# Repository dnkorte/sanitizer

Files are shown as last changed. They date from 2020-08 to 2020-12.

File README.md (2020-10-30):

# Hand Sanitizer Dispenser

<h1 align="center">
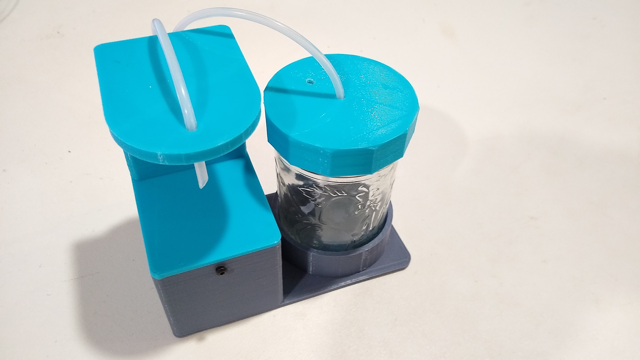
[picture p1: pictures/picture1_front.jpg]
Picture of Hand Sanitizer Dispenser
	<br>Hand Sanitizer Dispenser
</h1>

Hand Sanitizer (or soap) dispenser uses peristaltic pump to dispense fluid when Adafruit VCNL Optical Proximity Sensor observes hand under dispensing tube.  Code runs on an Adafruit ItsyBitsy 32u4 5v version (which may be powered by 12v Vbat) and is coded in Arduino IDE.  This is all packaged in a 3d printed container, and uses a standard Jelly Jar to hold the fluid.

Video of dispenser in action:  https://youtu.be/iYxsz3DUehM 

Photo Album: https://photos.app.goo.gl/EdRW3g8P56AdBAn6A

Thingiverse with STLs: https://www.thingiverse.com/thing:4636984

Some photos of the device are in the "photos" folder here on github; a larger collection is available in the linked photo album.  The Arduino software is in the "dispenser" folder here.  Printed Circuit board gerber files and schematic are in the "hardware" folder. STLs for 3d pringing are available in the "3d_printer_stls" folder and also on Thingiverse.   Note that it is important to use only the 5 Volt version of the 32u4 Itsy Bitsy, as this device allows a wider range of power input (the 5v 32u4 allows up to 16 volts input, but the normal ones only allow 6v input.  This circuit powers the Itsy Bitsy from the same 12v power block that runs the motor).

The device is setup such that when you initially put a hand into the dispense window it starts pumping at a high rate, then after a couple cycles it slows down for the balance of the hand-in-window period.  This helps to initially prime the pump/hose if its been sitting for a while, but doesn't over-deliver once its gotten started.  When the hand is removed it reverses the motor and sucks back some fluid to reduce drippage.

The device plays a series of beeps through the included speaker while it is dispensing.  

### Bill of Materials

| Description | Supplier | Notes |
| --- | --- | ----- |
| [ItsyBitsy 32u4 5v](https://www.adafruit.com/product/3677) | Adafruit | must be 5v version for power supply [Guide](https://learn.adafruit.com/introducting-itsy-bitsy-32u4/overview) |
| [TB6612 Motor Driver](https://www.adafruit.com/product/2448) | Adafruit | [Guide](https://learn.adafruit.com/adafruit-tb6612-h-bridge-dc-stepper-motor-driver-breakout) |
| [VCNL 4040 Lux/Proximity Sensor](https://learn.adafruit.com/adafruit-vcnl4040-proximity-sensor/) | Adafruit | [Guide](https://www.adafruit.com/product/4161)
| [2.1mm Barrel Jack](https://www.adafruit.com/product/610) | Adafruit |
| [Mini Oval Speaker](https://www.adafruit.com/product/3923) | Adafruit | note: will cut off connector and replace |
| [Peristaltic Pump 12v with hose](https://www.amazon.com/Peristaltic-Liquid-Dosing-Silicone-Tubing/dp/B075VN1QZM) | Amazon | includes 1m silicone tubing & 2 barbed connectors; 100 mL/min 300 mA |
| [12v 2A power supply with Barrel plug](https://www.amazon.com/TMEZON-Power-Adapter-Supply-2-1mm/dp/B00Q2E5IXW) | Amazon  |
| [2-pin Screw Terminal Block](https://www.amazon.com/dp/B01C3DGIBQ/) | Amazon | 2 pcs req'd; 3.5mm pitch |
| [47 uF Electrolytic Capacitor](https://www.adafruit.com/product/2194) | Adafruit | stand-up tubular, value not critical, just for DC blocking
| [Female Header Strip](https://www.adafruit.com/product/598) | Adafruit | need  to cut 2 14 pin sections |
| [Pin Header strip (male)](https://www.adafruit.com/product/392) | Adafruit | need to cut 3-pin, and 4-pin sections |
| [2-pin Dupont Connector body](https://www.amazon.com/Hilitchi-2-54mm-Headers-Connector-Housing/dp/B012EOO9Q0/) | Amazon | with female pins (note this assortment has 2- and 4- pin bodies as well as male pin header strip; you will need a [crimper](https://www.adafruit.com/product/350) to assemble these)|
| [4-pin Dupont Connector body](https://www.amazon.com/Hilitchi-2-54mm-Headers-Connector-Housing/dp/B012EOO9Q0/) | Amazon | with female pins |
| M3 x 8mm screws | Amazon | 12 pcs (lid-to-box, hose clamps to tower, tower-to-lid) |
| M3 x 6mm screws | Amazon | 4 pcs (to mount PCB) |
| M2.5 x 6mm screws | Amazon | 4 pcs (for Proximity Sensor) |
| [M3 Threaded Insert](https://www.mcmaster.com/94459A130/) | McMaster-Carr | 14 pcs (lid-to-box, hose clamps, pump, PCB-to-box) |
| [M2.5 Threaded Insert](https://www.amazon.com/Products-Insert-Heat-Sink-Injection/dp/B07HKT5W7S/) | Amazon | 4 pcs (for Proximity Sensor) |
| Glass Jelly Jar | local grocery | standard 1-pint jelly / jam jar as used for canning |

### Printed Circuit Board
<h1 align="center">
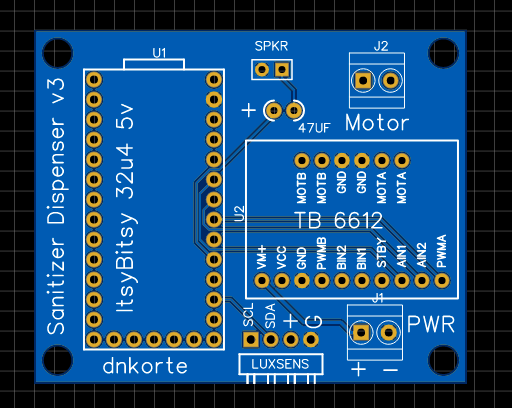
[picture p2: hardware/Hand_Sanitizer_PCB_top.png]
Picture of Hand Sanitizer Dispenser
	
</h1>

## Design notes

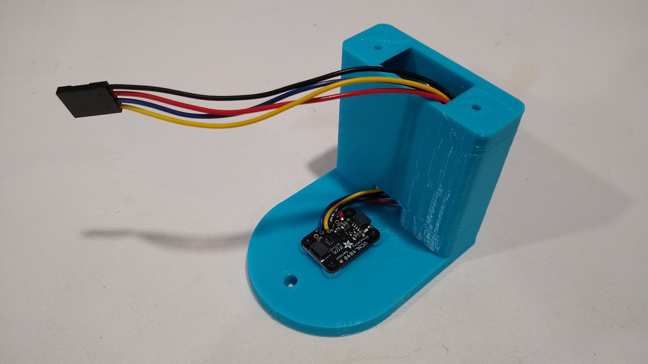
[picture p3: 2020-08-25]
pictures/picture5_riser.jpg

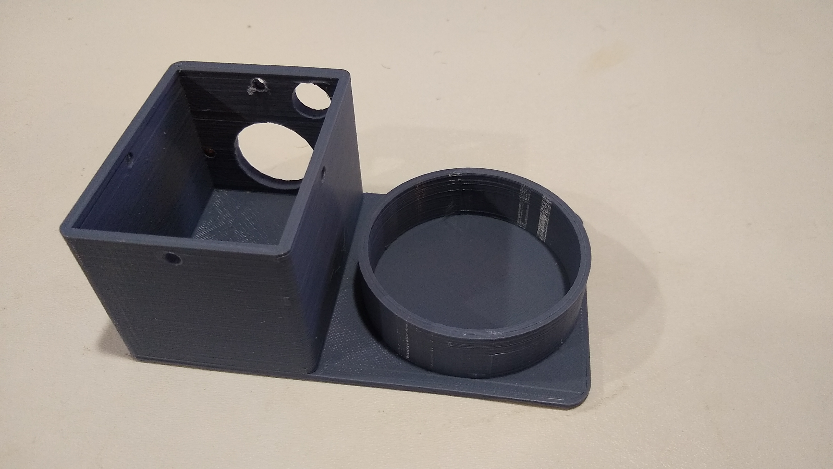
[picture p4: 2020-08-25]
pictures/picture6_box_bottom_riser.jpg

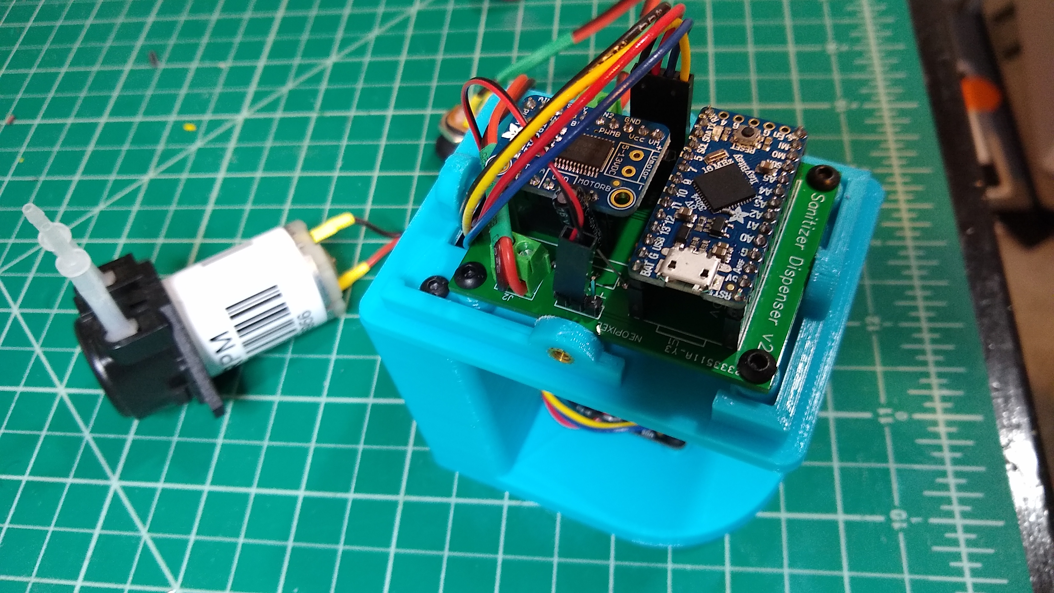
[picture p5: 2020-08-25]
pictures/picture4_pcb_closeup.jpg

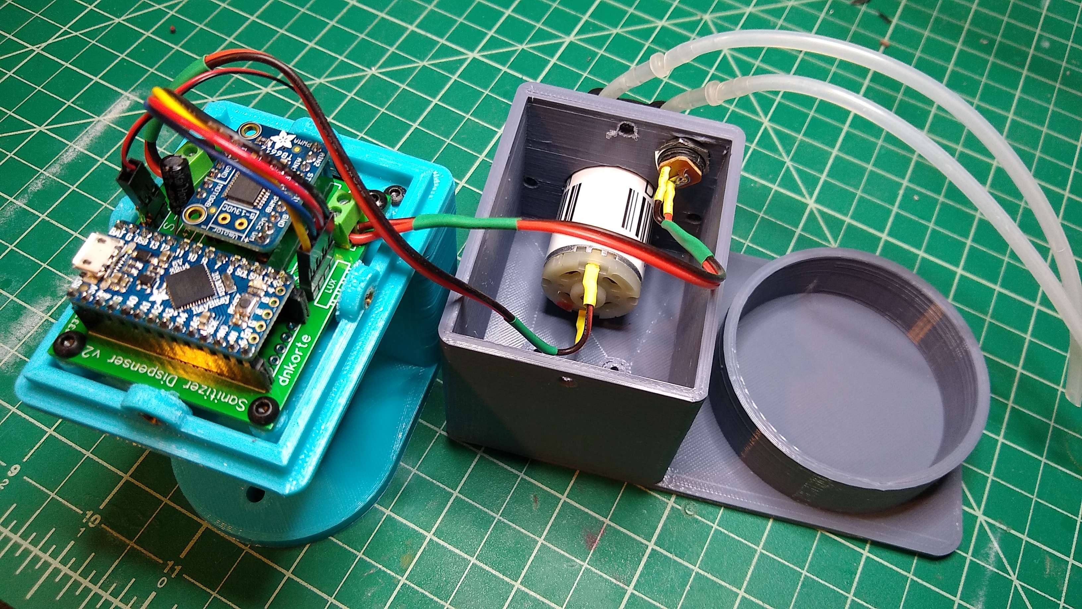
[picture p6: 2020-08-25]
pictures/picture3_internal.jpg

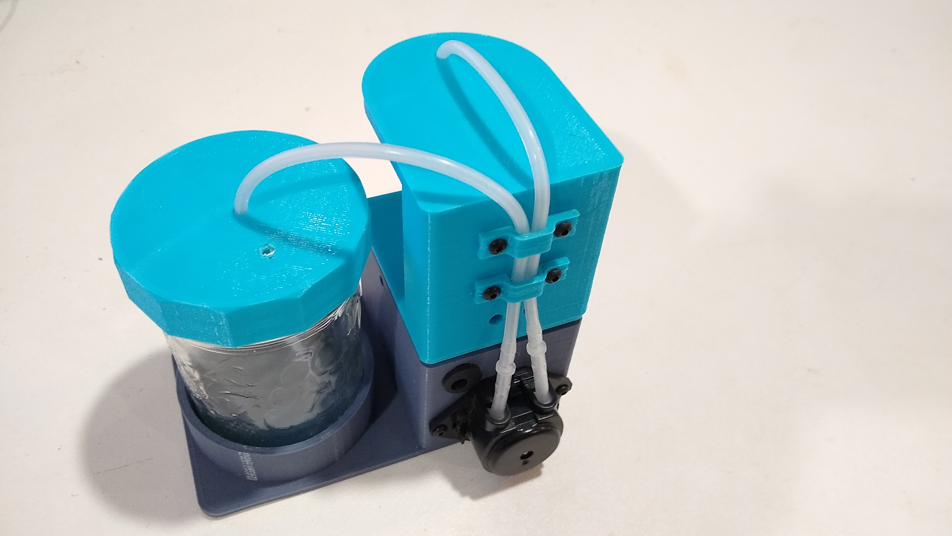
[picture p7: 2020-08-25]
pictures/picture2_back.jpg

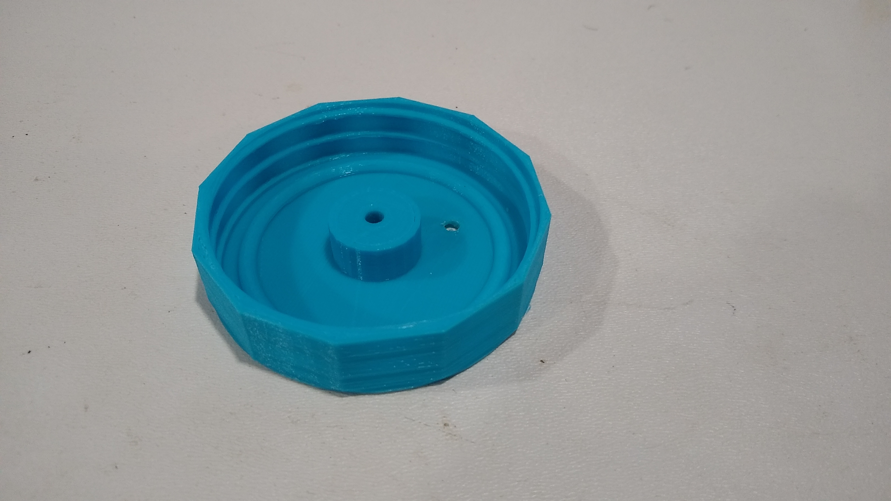
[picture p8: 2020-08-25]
pictures/picture6_jar_lid.jpg

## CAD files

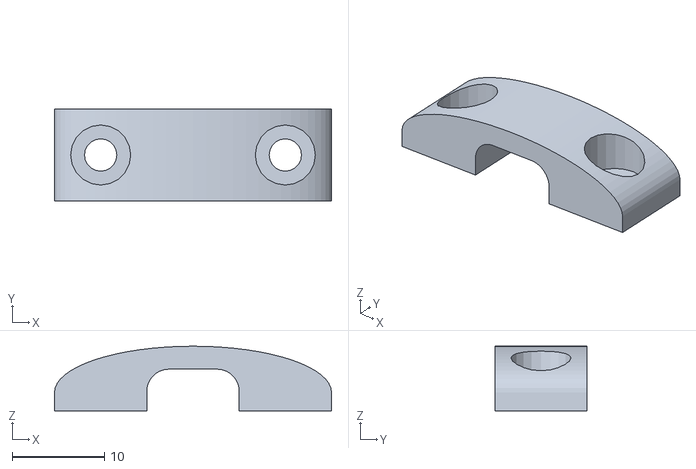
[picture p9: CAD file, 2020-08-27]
3d_printer_stls/tubing_clamp_v3.stl
30.0 x 10.0 x 7.00

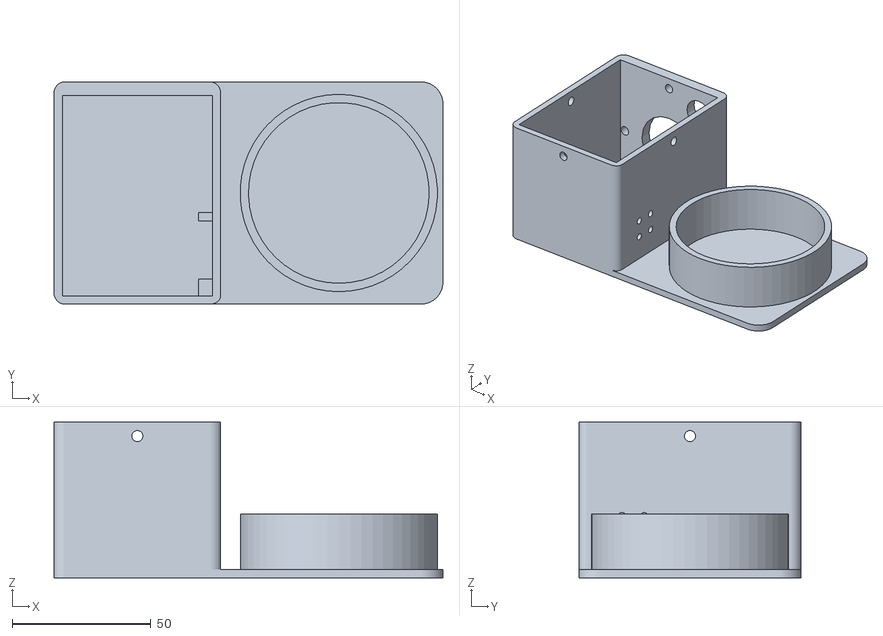
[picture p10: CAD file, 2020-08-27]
3d_printer_stls/base_v5.stl
140.0 x 80.0 x 56.0

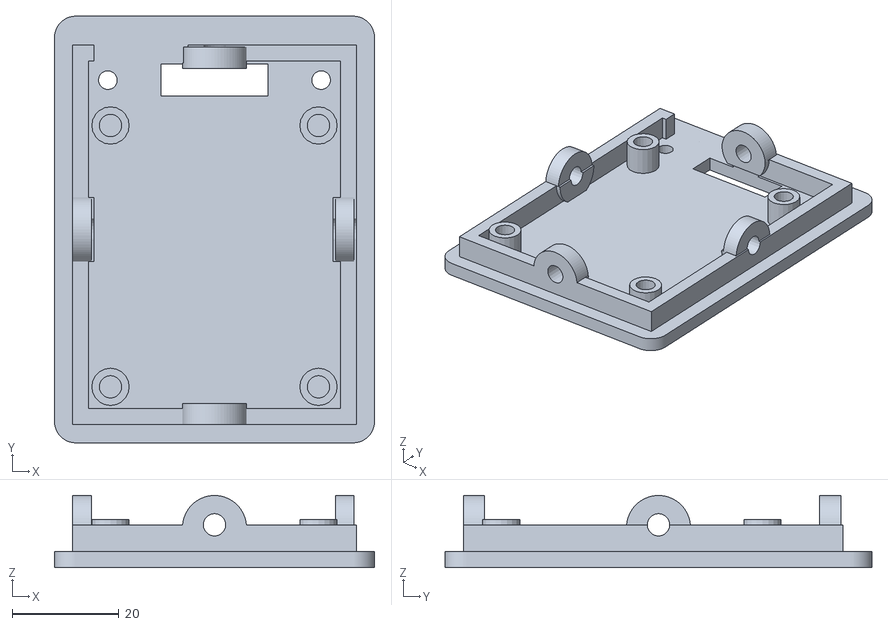
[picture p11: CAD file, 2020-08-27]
3d_printer_stls/lid_v6.stl
60.0 x 80.0 x 13.5

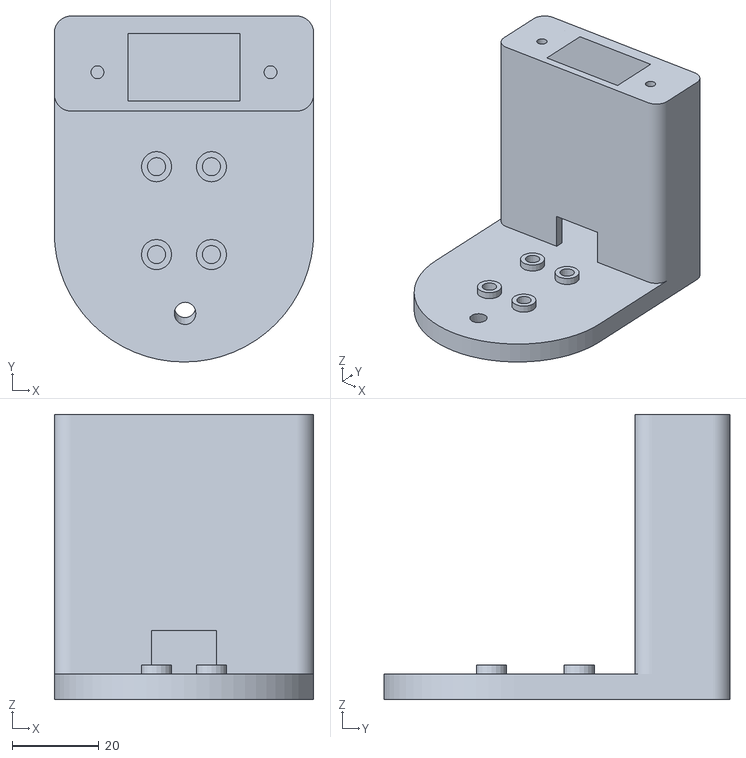
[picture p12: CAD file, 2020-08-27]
3d_printer_stls/tower_v3.stl
60.0 x 80.0 x 66.0

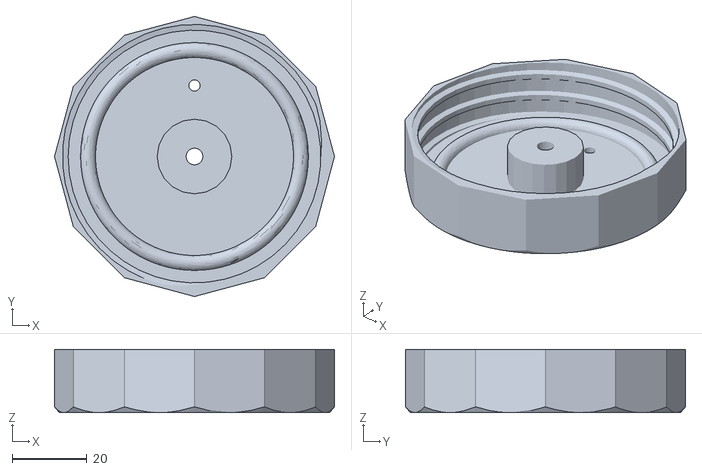
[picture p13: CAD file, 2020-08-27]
3d_printer_stls/jar_lid_v2.stl
75.0 x 75.0 x 17.0

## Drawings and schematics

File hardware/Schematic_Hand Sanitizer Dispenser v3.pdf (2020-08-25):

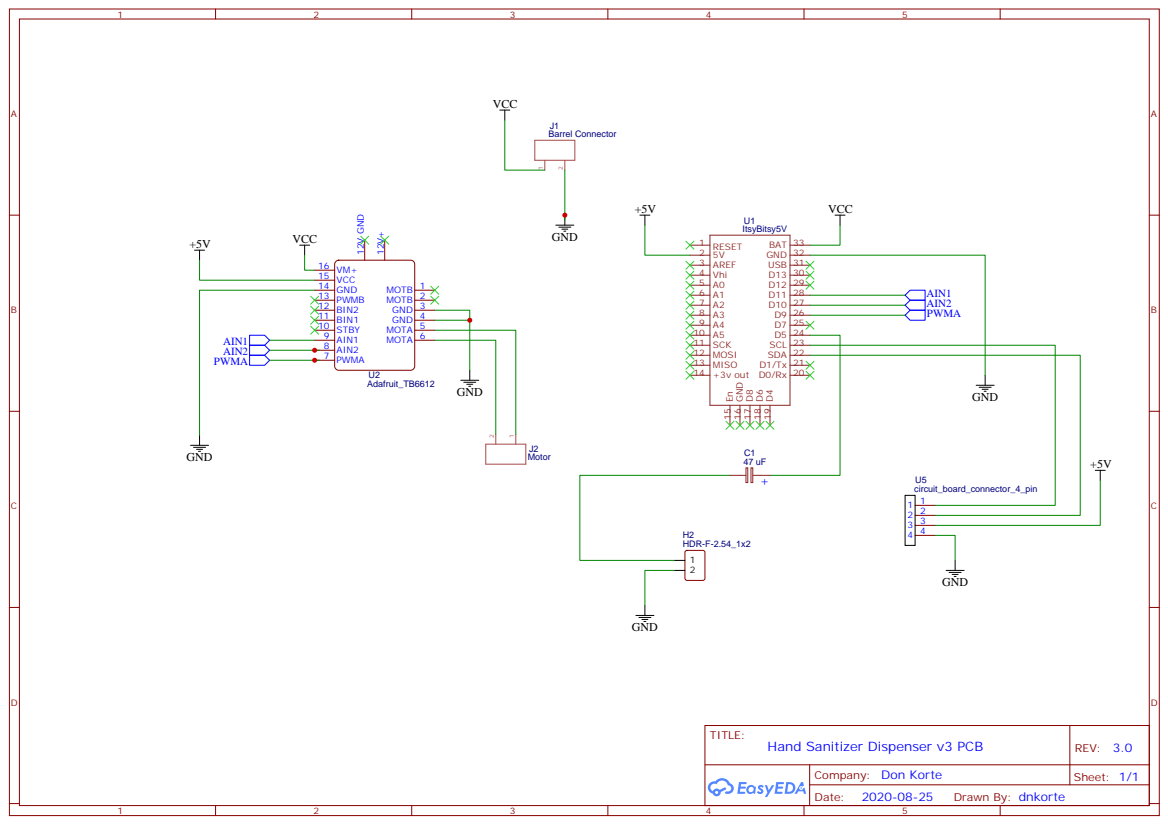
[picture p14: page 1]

BIN2 12 PWMB 13 GND 14 VCC 15 VM+ 16

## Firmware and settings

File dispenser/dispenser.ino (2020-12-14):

/*
 * dispenser.ino
 * 
 * Author(s):  Don Korte
 * Repository: https://github.com/dnkorte/sanitizer
 * Version: 1.0 Aug 25 2020; first working version
 * 
 * Hand Sanitizer (or soap) dispenser uses peristaltic pump to dispense fluid 
 * when Adafruit VCNL Optical Proximity Sensor observes hand under dispensing 
 * tube. Code runs on ItsyBitsy 32u4 5v version (which accepts 12v Vbat) and 
 * is coded in Arduino IDE. This is all packaged in a 3d printed box, and uses 
 * a standard Jelly Jar to hold the fluid.
 * 
 * Rev 30-Oct-2020 
 *  changed from 3-speed zones to 1-zone with pump speed that varies 
 *  according to duration of dispense -- it starts out fast, then after
 *  4 cycles it slows down for duration of dispense.  this reduces
 *  the amount of drippage
 * 
 * this code requires SparkFun TB6612FNG library for Arduino
 * https://github.com/sparkfun/SparkFun_TB6612FNG_Arduino_Library
 * https://github.com/sparkfun/SparkFun_TB6612FNG_Arduino_Library/blob/master/src/SparkFun_TB6612.h
 * https://github.com/sparkfun/SparkFun_TB6612FNG_Arduino_Library/blob/master/examples/MotorTestRun/MotorTestRun.ino
 * 
 * Adafruit TB6612 board Purchase Link: https://www.adafruit.com/product/2448
 * Adafruit Guide for TB6612: https://learn.adafruit.com/adafruit-tb6612-h-bridge-dc-stepper-motor-driver-breakout
 * (note i was unable to find an Adafruit library for this device running on Arduino IDE)
 * 
 * this code requires Adafruit library for VCLN 4040 Proximity Sensor
 * Guide:  https://learn.adafruit.com/adafruit-vcnl4040-proximity-sensor/overview
 * Purchase Link: https://www.adafruit.com/product/4161
 * 
 * 
 * MIT License
 *
 * Copyright (c) 2020 Don Korte
 * 
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
 * THE SOFTWARE IS PROVIDED "AS IS", WITHOUT WARRANTY OF ANY KIND, EXPRESS OR
 * IMPLIED, INCLUDING BUT NOT LIMITED TO THE WARRANTIES OF MERCHANTABILITY,
 * FITNESS FOR A PARTICULAR PURPOSE AND NONINFRINGEMENT. IN NO EVENT SHALL THE
 * AUTHORS OR COPYRIGHT HOLDERS BE LIABLE FOR ANY CLAIM, DAMAGES OR OTHER
 * LIABILITY, WHETHER IN AN ACTION OF CONTRACT, TORT OR OTHERWISE, ARISING FROM,
 * OUT OF OR IN CONNECTION WITH THE SOFTWARE OR THE USE OR OTHER DEALINGS IN THE
 * SOFTWARE. * 
 */

#include <Adafruit_VCNL4040.h>
#include <SparkFun_TB6612.h>
#define TONEPIN 5

// either 1 or -1 depending on motor wiring polarity
#define DIRECTION -1   

// duration of initial fast pumping allowance
#define ALLOWED_FAST_CYCLES 4   

// Pins for all inputs, keep in mind the PWM defines must be on PWM pins
#define AIN1 11
#define AIN2 10
#define PWMA 9
#define STBY 7

// these constants are used to allow you to make your motor configuration 
// line up with function names like forward.  Value can be 1 or -1
const int offsetA = 1;

// Initializing motors.  The library will allow you to initialize as many
// motors as you have memory for.  If you are using functions like forward
// that take 2 motors as arguements you can either write new functions or
// call the function more than once.
Motor motor1 = Motor(AIN1, AIN2, PWMA, offsetA, STBY);

Adafruit_VCNL4040 vcnl4040 = Adafruit_VCNL4040();

int  hand_prox;
bool dispensed_this_cycle, dispensed_last_cycle;

int  fast_cycles_left;

void setup() {
  vcnl4040.begin();
  fast_cycles_left = ALLOWED_FAST_CYCLES;
}

void loop() {  
  
  //Serial.print("Proximity:"); Serial.println(vcnl4040.getProximity());
  //Serial.println("");
  
  /*
   * note proximity value sits about 12-13 if no hand under sensor
   * its about 30 at midrange and 100-200 at very top
   *
   * note speed can range from -255 to +255; 
   * (-50) seems to be a pretty good compromise to avoid squirting
   * big messes vs getting enough quickly enough to satisfy, YMMV
   * 
   * change sign if necessary to account for motor wiring polarity
   * or hose routing
   */

  hand_prox = vcnl4040.getProximity();
  
  if (hand_prox < 15) {
    /* 
     *  no hand sensed, so just ensure motor is off
     */
    noTone(TONEPIN);
    motor1.drive(0);
    dispensed_this_cycle = false;
    fast_cycles_left = ALLOWED_FAST_CYCLES;
        
  } else {
    
    if (fast_cycles_left > 0) {
      fast_cycles_left--;
      /* 
       *  just starting to dispense, so go fast
       */
      tone(TONEPIN, 1500, 50);
      motor1.drive(90 * DIRECTION);      
      delay(500);
      motor1.drive(0);
      dispensed_this_cycle = true;
      delay(25);
    } else {
      /* 
       * we've been dispensing for a while, so slow down 
       */
      tone(TONEPIN, 1000, 50);
      motor1.drive(70 * DIRECTION);      
      delay(300);
      motor1.drive(0);
      dispensed_this_cycle = true;
      delay(100);
     }
    
  } 
  
  if (dispensed_last_cycle && !dispensed_this_cycle) {
      /*
       * when hand LEAVES, suck some fluid back to stop drips
       */
       motor1.drive( (-90) * DIRECTION );      
       delay(700);
       motor1.drive(0);       
  }

  
  dispensed_last_cycle = dispensed_this_cycle;

  /*
   * finally, ensure that there's at least a little
   * bit of delay this loop - just to give the 
   * processor a little time to breath...  :-)
   */
  if (!dispensed_this_cycle) {
    delay(50);
  }
}

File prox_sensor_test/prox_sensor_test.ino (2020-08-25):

/*
 * test program for Adafruit VCNL4040 optical prox sensor
 * this code is lifted (and slightly modified from)from the Adafruit Guide for that device
 * Guide:  https://learn.adafruit.com/adafruit-vcnl4040-proximity-sensor/overview
 * Purchase Link: https://www.adafruit.com/product/4161
 */

#include <Adafruit_VCNL4040.h>

Adafruit_VCNL4040 vcnl4040 = Adafruit_VCNL4040();


#define TONEPIN 5

void setup() {
  Serial.begin(115200);
  // Wait until serial port is opened
  while (!Serial) { delay(1); }

  Serial.println("Adafruit VCNL4040 Config demo");

  if (!vcnl4040.begin()) {
    Serial.println("Couldn't find VCNL4040 chip");
    while (1);
  }
  Serial.println("Found VCNL4040 chip");

  //vcnl4040.setProximityLEDCurrent(VCNL4040_LED_CURRENT_200MA);
  Serial.print("Proximity LED current set to: ");
  switch(vcnl4040.getProximityLEDCurrent()) {
    case VCNL4040_LED_CURRENT_50MA: Serial.println("50 mA"); break;
    case VCNL4040_LED_CURRENT_75MA: Serial.println("75 mA"); break;
    case VCNL4040_LED_CURRENT_100MA: Serial.println("100 mA"); break;
    case VCNL4040_LED_CURRENT_120MA: Serial.println("120 mA"); break;
    case VCNL4040_LED_CURRENT_140MA: Serial.println("140 mA"); break;
    case VCNL4040_LED_CURRENT_160MA: Serial.println("160 mA"); break;
    case VCNL4040_LED_CURRENT_180MA: Serial.println("180 mA"); break;
    case VCNL4040_LED_CURRENT_200MA: Serial.println("200 mA"); break;
  }
  
  //vcnl4040.setProximityLEDDutyCycle(VCNL4040_LED_DUTY_1_40);
  Serial.print("Proximity LED duty cycle set to: ");
  switch(vcnl4040.getProximityLEDDutyCycle()) {
    case VCNL4040_LED_DUTY_1_40: Serial.println("1/40"); break;
    case VCNL4040_LED_DUTY_1_80: Serial.println("1/80"); break;
    case VCNL4040_LED_DUTY_1_160: Serial.println("1/160"); break;
    case VCNL4040_LED_DUTY_1_320: Serial.println("1/320"); break;
  }

  //vcnl4040.setAmbientIntegrationTime(VCNL4040_AMBIENT_INTEGRATION_TIME_80MS);
  Serial.print("Ambient light integration time set to: ");
  switch(vcnl4040.getAmbientIntegrationTime()) {
    case VCNL4040_AMBIENT_INTEGRATION_TIME_80MS: Serial.println("80 ms"); break;
    case VCNL4040_AMBIENT_INTEGRATION_TIME_160MS: Serial.println("160 ms"); break;
    case VCNL4040_AMBIENT_INTEGRATION_TIME_320MS: Serial.println("320 ms"); break;
    case VCNL4040_AMBIENT_INTEGRATION_TIME_640MS: Serial.println("640 ms"); break;
  }


  //vcnl4040.setProximityIntegrationTime(VCNL4040_PROXIMITY_INTEGRATION_TIME_8T);
  Serial.print("Proximity integration time set to: ");
  switch(vcnl4040.getProximityIntegrationTime()) {
    case VCNL4040_PROXIMITY_INTEGRATION_TIME_1T: Serial.println("1T"); break;
    case VCNL4040_PROXIMITY_INTEGRATION_TIME_1_5T: Serial.println("1.5T"); break;
    case VCNL4040_PROXIMITY_INTEGRATION_TIME_2T: Serial.println("2T"); break;
    case VCNL4040_PROXIMITY_INTEGRATION_TIME_2_5T: Serial.println("2.5T"); break;
    case VCNL4040_PROXIMITY_INTEGRATION_TIME_3T: Serial.println("3T"); break;
    case VCNL4040_PROXIMITY_INTEGRATION_TIME_3_5T: Serial.println("3.5T"); break;
    case VCNL4040_PROXIMITY_INTEGRATION_TIME_4T: Serial.println("4T"); break;
    case VCNL4040_PROXIMITY_INTEGRATION_TIME_8T: Serial.println("8T"); break;
  }

  //vcnl4040.setProximityHighResolution(false);
  Serial.print("Proximity measurement high resolution? ");
  Serial.println(vcnl4040.getProximityHighResolution() ? "True" : "False");

  Serial.println("");

}

void loop() {
  int hand_prox;
  
  Serial.print("Proximity:"); Serial.println(vcnl4040.getProximity());
  Serial.print("Ambient light:"); Serial.println(vcnl4040.getLux());
  Serial.print("Raw white light:"); Serial.println(vcnl4040.getWhiteLight());
  Serial.println("");


  hand_prox = vcnl4040.getProximity();
  if (hand_prox < 16) {
    noTone(TONEPIN);
  } else if (hand_prox < 20) {
      tone(TONEPIN, 1000, 100);
      delay(150);
  } else if (hand_prox < 30) {
      tone(TONEPIN, 2000, 100);
      delay(150);
  } else if (hand_prox > 50) {
      tone(TONEPIN, 3000, 100);
      delay(150);
  }

  
  delay(50);
}

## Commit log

2020-08-25 added schematic and gerbers
2020-08-27 added 3dprinter stls
    [base_v5.stl, jar_lid_v2.stl, lid_v6.stl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]
2020-08-28 started BOM
2020-08-28 updated BOM
2020-10-24 added pullback (suck) after hand is removed to reduce drips; also added high speed pump when hand superclose to help prime pump if unused for a long time
